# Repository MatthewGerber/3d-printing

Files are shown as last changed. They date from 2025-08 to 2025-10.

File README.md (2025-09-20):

General information about my experience with 3D printing. A list of personal projects is 
[here](https://matthewgerber.github.io/raspberry-py/cad-parts.html), and the model files are available 
[here](https://www.printables.com/@MatthewGerbe_3143168/models).

# CAD software

I started out with [FreeCAD](https://www.freecadweb.org/). I was impressed by the range of capabilities 
that comes with the software and the quality with which they are delivered---at least initially. Everything worked well 
for small parts and the initial phases of the larger arm project. However, as the design grew, the tree-structure 
representation of design elements became unwieldy. It was difficult to predict how the tree would rearrange following
an operation. Ultimately, a bug surfaced in the FreeCAD software, and I was unable to undo and recover my design. I 
started looking elsewhere and found [Autodesk Fusion 360](https://www.autodesk.com/products/fusion-360/personal), which 
can be obtained free of charge for personal use. I was, and still am, quite new to CAD; however, Fusion 360 is obviously 
a top-notch product. Everything just works. The operations are stunningly intuitive and well-crafted. It is difficult to 
imagine a reason for looking elsewhere except, of course, for the facts that the free version cannot be used 
commercially and the commercial version is quite expensive.

The small deboss labels on various components contain the Fusion 360 version numbers of the design file. This is a 
handy way to keep track of the design file version used to print each component, particularly when diagnosing issues, 
updating the design, and printing new versions. I use the 
[ParametricText](https://parametrictext.readthedocs.io/en/stable/) add-in to automatically update the version numbers 
when saving the design file.

# Mesh Slicer

[UltiMaker Cura](https://ultimaker.com/software/ultimaker-cura) is a simple tool with a single purpose:
slice the mesh outputs of a mesh model into horizontal layers of 3D printer instructions. I used Cura successfully for 
quite a while, but eventually ran into issues with filament stringing. After trying many (many) alternative 
configurations, I found that the [PrusaSlicer](https://www.prusa3d.com/) default settings are very effective, and I've
been using this tool ever since.

# 3D Printer

With endless options on the market it can be difficult to choose; however, at under $200 (in 2022) with generally 
quite positive reviews, it was difficult to get past the [Creality Ender 3](https://www.creality.com/products/ender-3-3d-printer). It was simple to assemble and has been 
cranking out high-quality pieces since the start.

## Web Interface

I use [OctoPrint](https://octoprint.org) with my Raspberry Pi as an efficient and easy way to manage print jobs. 
See [here](https://matthewgerber.github.io/raspberry-py/octoprint.html) for tips on configuring OctoPrint on the Pi.

## Automatic Bed Leveling

I added the [CR Touch Automatic Leveling Kit](https://www.amazon.com/Creality-Leveling-Compatible-Mainboard-Printer/dp/B098LQ9WPX/ref=sr_1_3?th=1) 
to my Ender 3. The sensor comes with a mounting bracket for the Ender 3; however, it isn't truly designed for this 
model, and I had previously replaced the hot end with [something different](https://www.amazon.com/Authentic-Creality-Assembled-Aluminum-Hotend/dp/B082XXRT78/ref=sr_1_2_sspa).
As a result, the sensor was mounted too far above the bed, which caused the hot end to drop down into the bed. After 
much experimenting and searching, I found that the sensor needed to be offset down toward the bed in order for 
everything to work. I did this by adding spacers as shown below:

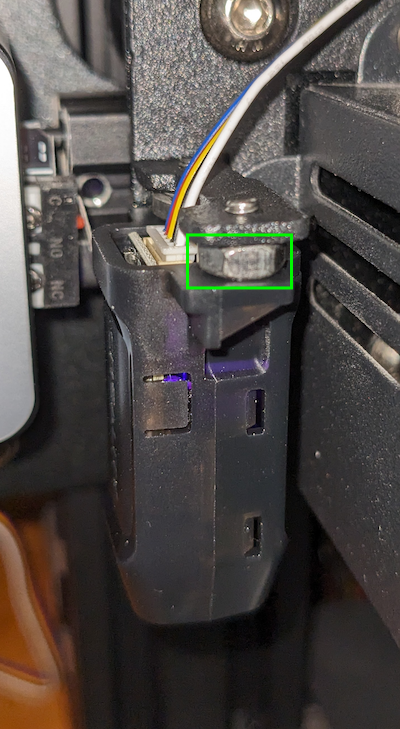
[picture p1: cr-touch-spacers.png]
cr-touch-spacers


After installing the hardware, flash the printer with the correct firmware [here](https://www.creality.com/products/cr-touch-auto-leveling-kit).
Download the firmware bundle prefixed with the printer name (e.g., "Ender-3 CR Touch Firmware" for an Ender 3 printer, or 
"Ender-3 V2 CR Touch Firmware" for an Ender 3 V2 printer). Within the bundle, select the board version. Note that 4.2.2 is 
an early board that requires a special adapter to plug the bed leveling probe into, whereas the 4.2.7 board has a direct 
connection for the probe. Clear an SD card and place the firmware binary onto the card as the only file. Name the file 
"firmware.bin", insert the SD card, and turn the printer off/on. The display should indicate that the firmware has been 
updated. Sometimes this is finicky, and the board doesn't take the firmware. Renaming the file "firmware-123.bin" or 
"Ender 3 firmware.bin" might work. The steps for calibrating the leveling probe's z-offset are as follows:

1. Auto-home the printer.
2. Move the z-axis to identify the appropriate z-offset using a sheet of A4 paper for thickness. Note the z-offset 
   that causes the nozzle to just slightly grab the paper. Call this `adjustment`.
3. Auto-home the printer again.
4. Access the leveling probe's z-offset and note its value. Call this `current`. Then set the leveling probe's 
   z-offset to `current + adjustment`.
5. Save the configuration settings.
6. Level the bed. The hot end should be in the correct position above the bed, with the z-value showing 0.0 on the 
   printer display and a very small gap between the nozzle and bed.
7. Add `G28 G29` to your slicer's g-code preamble. The `G28` (home) command is probably already present, in which case
   you just tack on `G29` (level bed).
8. Octoprint has a [bed leveling visualizer plugin](https://plugins.octoprint.org/plugins/bedlevelvisualizer), which displays the bed mesh as shown below:
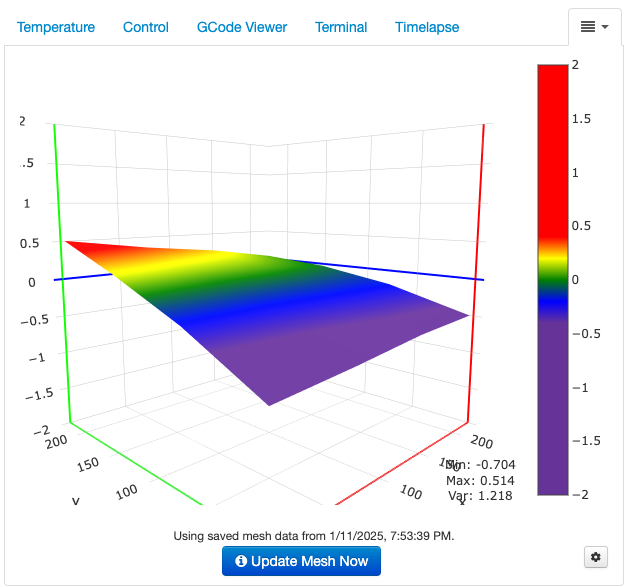
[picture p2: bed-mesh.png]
bed-mesh
  
9. Add `G28 G29` to your slicer's g-code preamble. The `G28` (home) command is probably already present, in which case
  you just tack on `G29` (level bed).

## Extruder-Step Calibration

After installing the new bed leveling firmware above, I kept running into under-extrusion issues. It took a while to 
realize that the new firmware was configured with a lower extrusion rate than the stock Ender 3 firmware. The process 
for calibrating the extrusion rate (or e-steps) is as follows:

1. Use the menu options to manually extrude 10cm (100mm) of filament. Here, 100mm is `expected mm`.
2. Measure how many mm of filament is actually extruded, and call this `actual mm`. If `actual mm` equals 
   `expected mm` exactly, then there is no need to calibrate the e-steps. If `actual mm` does not equal `expected mm`, 
   then proceed.
3. View the extruder's current `steps/mm` value. This is the number of steps that the printer expects it takes to 
   extrude 1mm of filament. Multiply `steps/mm * expected mm` to obtain `steps taken`, the number of steps the 
   extruder actually took to extrude `actual mm`. 
4. Calculate `steps taken / actual mm` to obtain the calibrated steps/mm value. Enter this into the settings. For
   example:
     1. Under-extrusion:  (81 steps/mm * 100mm expected) / (93mm actual) = 87.097 steps/mm calibrated
     2. Over-extrusion:  (81 steps/mm * 100mm expected) / (117mm actual) = 69.231 steps/mm calibrated
5. Python function to obtain the calibrated steps/mm:
   ```python
   def calibrate(
       expected_mm: float, 
       actual_mm: float, 
       steps_per_mm: float
   ) -> float: 
       return (steps_per_mm * expected_mm) / actual_mm
   ```
   
## Bed Update with Direct-drive Extrusion 
In the end, the automatic bed leveling update did not work very well. Some prints did okay, but others had issues when 
printing over the entire print bed. I ended up reverting back to the stock Ender 3 firmware as follows:

1. Visit the Creality Cloud [firmware site](https://www.crealitycloud.com/downloads/firmware/ender-series/ender-3).
2. Download `Ender-3Marlin2.0.6HW4.2.2 GD Version firmware`, as my Ender 3 has the 4.2.2 mainboard with the GD chip.
3. After flashing the firmware, the default language is Chinese. The language menu is second from bottom in the main
   interface.
4. Recalibrate the extrusion stepper motor (see above).

I updated to [a glass bed](https://www.amazon.com/Creality-Ender-Glass-Upgraded-235x235x4mm/dp/B07RD6D2ZQ/), which is
very flat, and also to [a direct-drive](https://www.amazon.com/dp/B09KG8MMQ2) adapter for the extrusion motor. This
has been working well.

## Changing the Bowden Tube and Nozzle

This is particularly relevant when the extruder stepper motor is skipping, the extruder gear is slipping on the 
filament, or the printer is under-extruding.
1. Remove the nozzle:  The flat end should be clean without any filament sitting on top, which might indicate that the 
   bowden tube isn't tightly seated against the nozzle entry within the hot end.
2. Replace the bowden tube.
   1. Replace the tube couplings in the extruder and hot end to ensure they will properly grab the new tube. 
   2. Tighten the nozzle.
   3. Loosen the nozzle 3/4 a turn.
   4. Insert the bowden tube firmly and fully into the hot end coupling.
   5. Heat the hot end.
   6. Tighten the nozzle, which seats the bowden tube firmly against the nozzle.
   7. Trim the tube to length for the extruder so that it can easily reach all print positions.
   8. Insert the bowden tube firmly and fully into the extruder coupling.
   9. Level the bed if needed.

## Heat Creep

Perhaps related to the new hot end mentioned above, I started having serious trouble with filament becoming stuck in 
the heat sink. Forums are littered with discussions of heat creep, with solutions ranging across filament drying, slicer 
settings (extrusion speeds and distances), cooling fans, and extruder upgrades. In my case, upgrading [the hot-end fan](https://www.amazon.com/dp/B0B1V52WGP?ref=ppx_yo2ov_dt_b_fed_asin_title&th=1) (\$13)
and [converting the extruder to direct drive](https://www.amazon.com/UniTak3D-Upgrade-Conversion-Compatible-Extruder/dp/B09KG8MMQ2/ref=sr_1_1_sspa) (\$15)
solved my problems.

# Printing Terrain

* [Terrain2STL](https://jthatch.com/Terrain2STL/)
* [Prusa Blog tips](https://blog.prusa3d.com/how-to-print-maps-terrains-and-landscapes-on-a-3d-printer_29117/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)

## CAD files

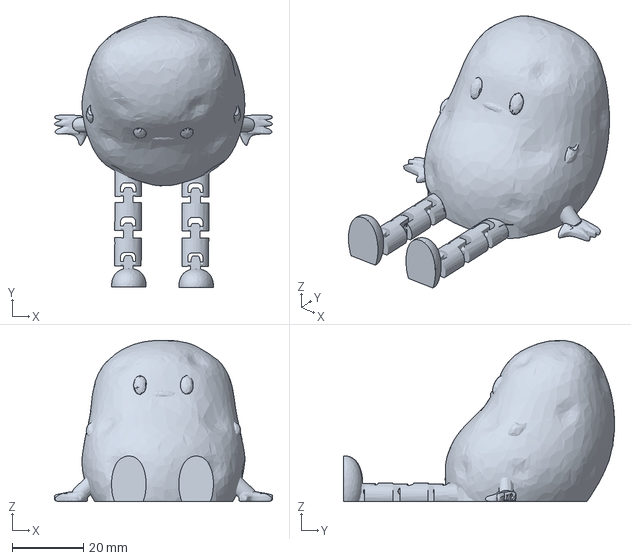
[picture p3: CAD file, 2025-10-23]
potato-buddy.3mf
61.1 x 76.0 x 45.1 mm

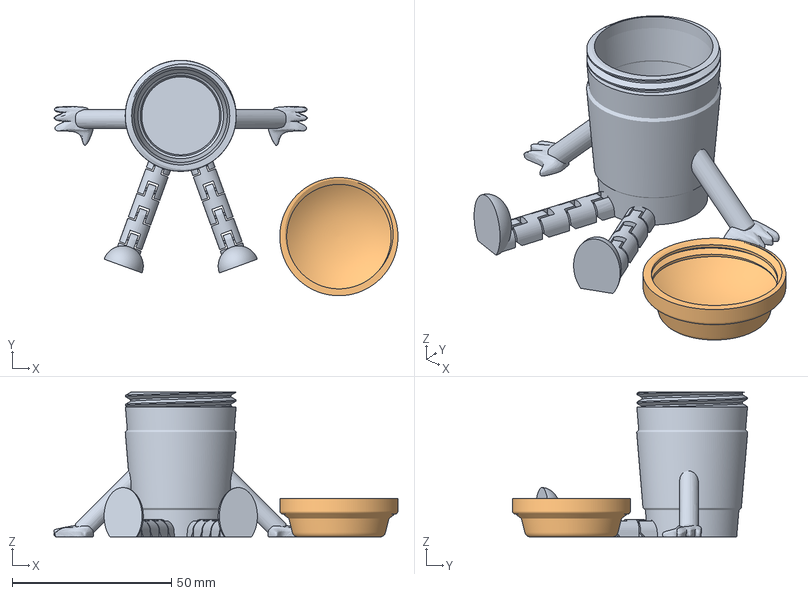
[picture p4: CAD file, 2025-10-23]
coffee-buddy.3mf
108.1 x 73.9 x 45.5 mm
flexi-coffee-buddy.stl
flexi-coffee-buddy-lid.stl

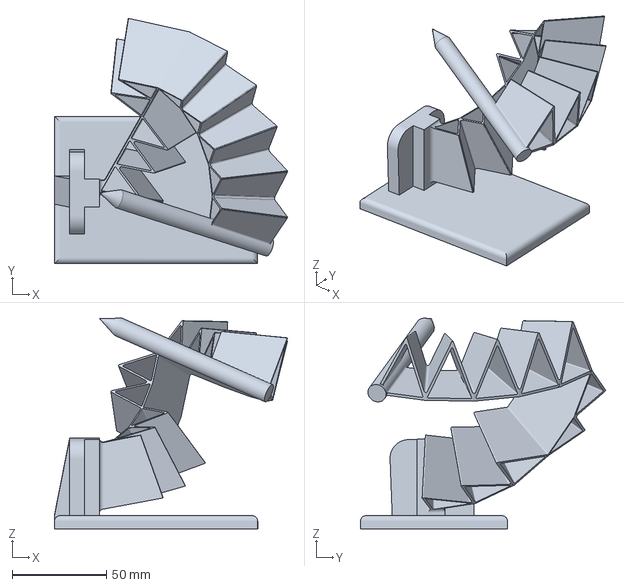
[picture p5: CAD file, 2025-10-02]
spherical-flexure-joint.3mf
123.8 x 130.3 x 111.9 mm

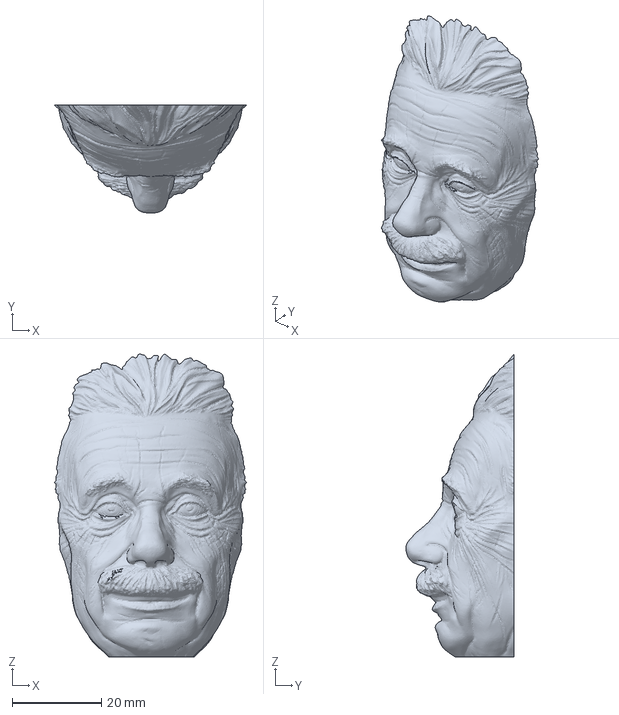
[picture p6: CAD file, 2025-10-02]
einstein-vase-face.3mf
43.0 x 24.2 x 67.8 mm

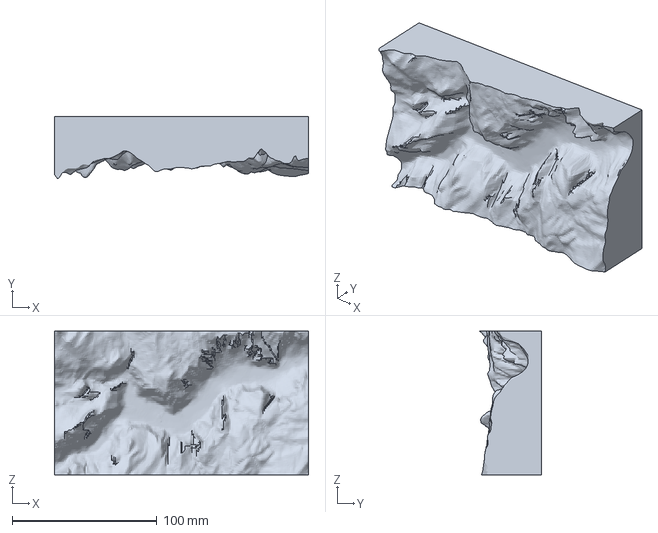
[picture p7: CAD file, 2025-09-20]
yosemite-valley.3mf
175.5 x 42.8 x 99.2 mm

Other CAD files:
yosemite-valley.stl

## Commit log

2025-08-25 Migrate some content from raspberry-py.
2025-09-20 Add Yosemite Valley.
    [yosemite-valley.3mf, yosemite-valley.stl]
2025-09-25 Add model.
    [coffee-buddy.3mf, einstein-vase-face.3mf]
2025-10-02 Add projects.
    [coffee-buddy.3mf, einstein-vase-face.3mf, spherical-flexure-joint.3mf]
2025-10-23 Add models.
    [coffee-buddy.3mf, potato-buddy.3mf]
